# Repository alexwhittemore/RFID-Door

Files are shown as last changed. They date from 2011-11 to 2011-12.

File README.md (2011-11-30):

RFID Door Lock
==============

This project centers around a [Parallax RFID reader](http://www.parallax.com/tabid/768/ProductID/114/Default.aspx) and an Arduino for reading 125khz RFID tags as a means of authentication for opening a deadbolt. The main PCB holds the barebones Arduino-compatible clone, a socket for a Digi Xbee module for communication with a home automation network or a computer, and power circuitry. It has connectors for the RFID module, a standard hobby servo to actuate the deadbolt, and a magnetic reed switch to sense whether or not the door is presently closed. It also has a header which breaks out all power connections, such that external 5V and 3.3V sources can be used.

RFID Reader
-----------

The Parallax RFID Reader above from Grand Idea Studio and Parallax is used. Both SOUT and /ENABLE are connected to the Arduino, and it is intended that a software serial port will be used (since the hardware serial is used elsewhere for communication and programming). Given this configuration, the RFID header is pin-compatible with the [new RFID reader/writer from Parallax](http://www.parallax.com/Store/Accessories/CommunicationRF/tabid/161/ProductID/688/List/0/Default.aspx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,ProductName) should that be desired in the future.

Arduino
-------

A barebones Arduino is implemented with a PDIP AVR socket (ATMega8/168/328 compatible) and an external 16MHz crystal. Arduino pins 0,1 are used for a hardware UART connection to the Xbee module. Pins 2,3 are connected to RFID SOUT and /ENABLE, respectively, usable either as GPIO or software serial. Pin 5 is used to drive the servo motor signal. AD 0 is used to sense the door open magnetic reed switch. Pull up and pull down resistor footprints are included, to be populated in accordance with the use of a normally open or normally closed reed switch. 

Additionally, a reset switch and an ISP programming header are included for users who may wish to program the chip either without the Arduino environment or simply without removing the chip from the board.

Xbee
----

A socket is included for use with a Digi Xbee module. These should all be pin-compatible across series 1/2/pro units as well as 2.4GHz/900MHz, and only the power, reset, and serial pins are utilzed. Installing this optional module allows for remote programming (I think?) as well as communication with the rest of a home automation network or a central computer. Ideas for this feature are: dynamic updating of the access list, access logging, internet-based access interface (unlock the door from your smart phone!). A reset button for the Xbee is also implemented, as is necessary for remote updating.

Level Translation
-----------------

The Xbee module is 3.3v and the Arduino is 5v, so level translation on the UART lines is necessary. The method used in the Xbee shield for Arduino is a series 10kOhm resistor on the Arduino Tx/Xbee Rx line such that the ESD diodes in the Xbee aren't overwhelmed with 20mA out of the Arduino. There is no translation on the Xbee Tx/Arduino Rx, with the expectation that 3.3v will be sufficient for a logic 'High' on the Arduino. This scheme may be used for parts count/cost reduction by solder bridging SJ1 and populating R3.

Alternately, footprints are included for On Semi MC74VHC1GT126 level non-inverting buffers. These will accurately translate 3.3V inputs to 5V outputs and vice-versa, where any input 0-10V is acceptable and 'High' output = Vdd. Populate these and leave SJ1 and R3 unbridged/unpopulated for full level translation.

Finally, headers on both input and output sides of level translation are included for ease of debugging.

Power
-----

Regulators are included with appropriate bypassing for 5V and 3.3V supplies. They are cascaded - a Vin pin is provided to supply power to be regulated down to 5V, then the 3.3V regulator takes its input from this 5V line:

Vin->`7805 Regulator`--5V+USB-->`REG103`-->3.3V

Therefore, the 5V regulator may be populated, and simply won't be used if Vin isn't supplied. However, if both external 5V and 3.3V supplies are used, the 3.3V regulator MUST be unpopulated! A USB Mini-B connector is also provided to optionally supply 5V power. Note that there is NO protection of ANY kind - this is intended only for use with dumb wall chargers or CAREFUL use supplying power from a computer. That is, the 5v regulator MUST NOT have power to it, or there could be damage!

Additionally, a REG103 from Burr-Brown (TI) is used as the 3.3V regulator. It's not a conventional part in the hobbyist spectrum (It's not used by Sparkfun/Dangerous Prototypes/OpenPilot/anyone else) - I just happened to have some. But they're inexpensive and highly available on Digikey and Mouser.

Software
--------

I haven't written it yet. But if you get to it before I do, it's a pretty standard mishmash of the SoftwareSerial library, some demo code for the RFID reader, and standard UART for the Xbee.

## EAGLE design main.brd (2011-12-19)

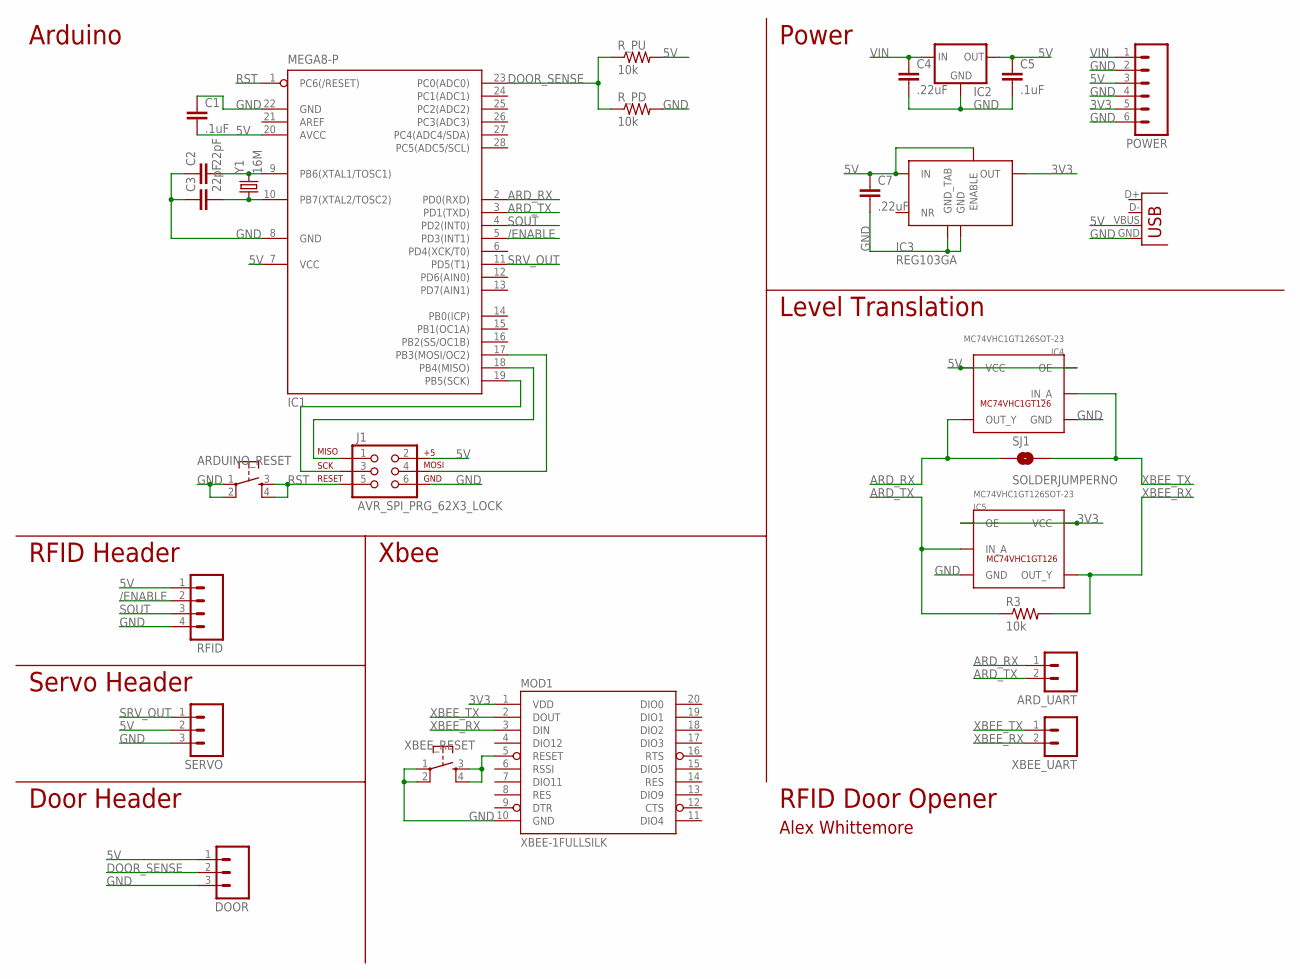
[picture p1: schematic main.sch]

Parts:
ARDUINO_RESET: TAC_SWITCHPTH; TACTILE-PTH
ARD_UART: M02LOCK_LONGPADS; 1X02_LOCK_LONGPADS
C1, C5: .1uF; 0805
C2, C3: 22pF; 0805
C4, C7: .22uF; 0805
DOOR: M03LOCK; 1X03_LOCK
IC1: MEGA8-P; DIL28-3
IC2: V_REG_78XX-TO-220; TO-220-ALT
IC3: REG103GA; SOT223-5
IC4, IC5: MC74VHC1GT126SOT-23; SOT23-5L
J1: AVR_SPI_PRG_62X3_LOCK; 2X3_LOCK
MOD1: XBEE-1FULLSILK; XBEE
POWER: M06LOCK; 1X06_LOCK
R3: 10k; 0805
RFID: M04LOCK_LONGPADS; 1X04_LOCK_LONGPADS
R_PD: 10k; 0805
R_PU: 10k; 0805
SERVO: M03LOCK; 1X03_LOCK
SJ1: SOLDERJUMPERNO; SJ_2S-NO
X1: USB-SMD-NS; USB-MINIB-NOSTOP
XBEE_RESET: TAC_SWITCHPTH; TACTILE-PTH
XBEE_UART: M02LOCK_LONGPADS; 1X02_LOCK_LONGPADS
Y1: 16M; HC49UP

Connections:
3V3: IC3.2 (OUT), IC5.1 (OE), IC5.5 (VCC), MOD1.1 (VDD), POWER.5
5V: C1.2, C5.1, C7.1, DOOR.1, IC1.7 (VCC), IC1.20 (AVCC), IC2.OUT, IC3.1 (IN), IC3.5 (ENABLE), IC4.1 (OE), IC4.5 (VCC), J1.2, POWER.3, RFID.1, R_PU.2, SERVO.2, X1.VBUS
/ENABLE: IC1.5 (PD3(INT1)), RFID.2
ARD_RX: ARD_UART.1, IC1.2 (PD0(RXD)), IC4.4 (OUT_Y), SJ1.1
ARD_TX: ARD_UART.2, IC1.3 (PD1(TXD)), IC5.2 (IN_A), R3.1
DOOR_SENSE: DOOR.2, IC1.23 (PC0(ADC0)), R_PD.1, R_PU.1
GND: ARDUINO_RESET.1, ARDUINO_RESET.2, C1.1, C2.1, C3.1, C4.2, C5.2, C7.2, DOOR.3, IC1.8 (GND), IC1.22 (GND), IC2.GND, IC3.3 (GND), IC3.TAB (GND_TAB), IC4.3 (GND), IC5.3 (GND), J1.6, MOD1.10 (GND), POWER.2, POWER.4, POWER.6, RFID.4, R_PD.2, SERVO.3, X1.GND, XBEE_RESET.1, XBEE_RESET.2
ISP_MISO: IC1.18 (PB4(MISO)), J1.1
ISP_MOSI: IC1.17 (PB3(MOSI/OC2)), J1.4
ISP_SCK: IC1.19 (PB5(SCK)), J1.3
unnamed: C2.2, IC1.9 (PB6(XTAL1/TOSC1)), Y1.2
unnamed: C3.2, IC1.10 (PB7(XTAL2/TOSC2)), Y1.1
RST: ARDUINO_RESET.3, ARDUINO_RESET.4, IC1.1 (PC6(/RESET)), J1.5
SOUT: IC1.4 (PD2(INT0)), RFID.3
SRV_OUT: IC1.11 (PD5(T1)), SERVO.1
VIN: C4.1, IC2.IN, POWER.1
XBEE_RST: MOD1.5 (RESET), XBEE_RESET.3, XBEE_RESET.4
XBEE_RX: IC5.4 (OUT_Y), MOD1.3 (DIN), R3.2, XBEE_UART.2
XBEE_TX: IC4.2 (IN_A), MOD1.2 (DOUT), SJ1.2, XBEE_UART.1

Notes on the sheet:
Level Translation
Power
Arduino
Xbee
RFID Header
Servo Header
Door Header
RFID Door Opener
Alex Whittemore

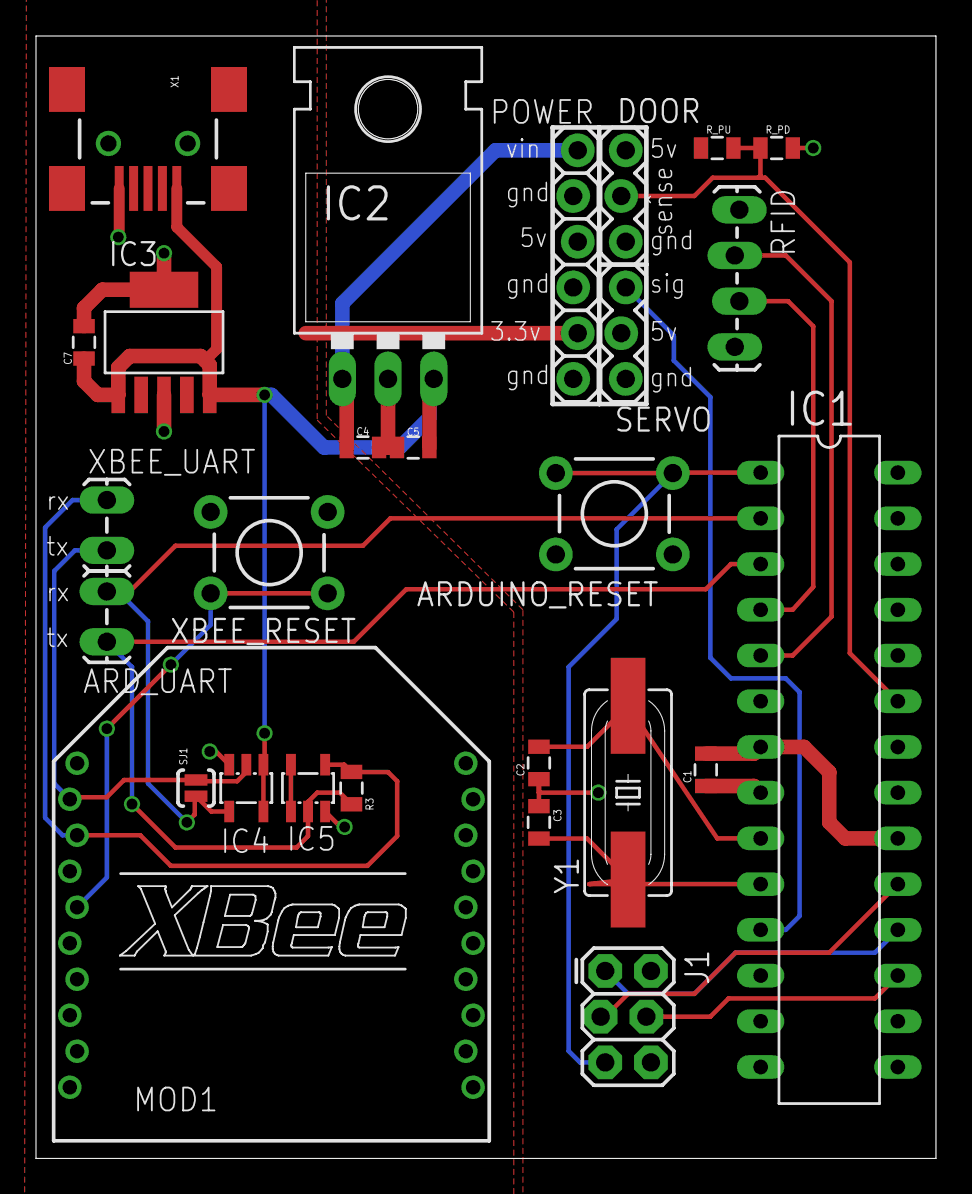
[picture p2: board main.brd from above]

Board: 2 copper layers, 50.0 x 62.4 mm, 27 parts (0 on the bottom side), 19 nets.

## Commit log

2011-11-30 Initial Commit
    Included is a more-or-less complete schematic, a preliminary board
    layout, and a readme to describe the project on Github.
    [main.brd, main.sch]
2011-12-01 Significantly reduced layout size to fit within 10x5cm
    Minor schematic modifications to support small board layout, large
    board modifications. TODO: Lots of silk screen clean up.
    [main.brd, main.sch]
2011-12-19 Converted to new Eagle V6 XML format
    [main.brd, main.sch]
